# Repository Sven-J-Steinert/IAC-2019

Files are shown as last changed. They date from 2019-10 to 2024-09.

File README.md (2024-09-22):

# Showcase for Satellite Routines
Developed for Telespazio VEGA. Presented on the International Astronautical Congress ( 2019 | Washington, D.C., USA )<br>
This setup consists of 3 parts: The [Orbiter](#orbiter) that is circling around the [Groundstation](#groundstation) and the [Node](#node) that connects both to an internet endpoint. Sending commands to the Orbiter as well as pulling the Telemetry from it is only possible while it is in sight of view of the satellite dish. This creates a connected and disconnected timespan in the periodic circling.

# Orbiter
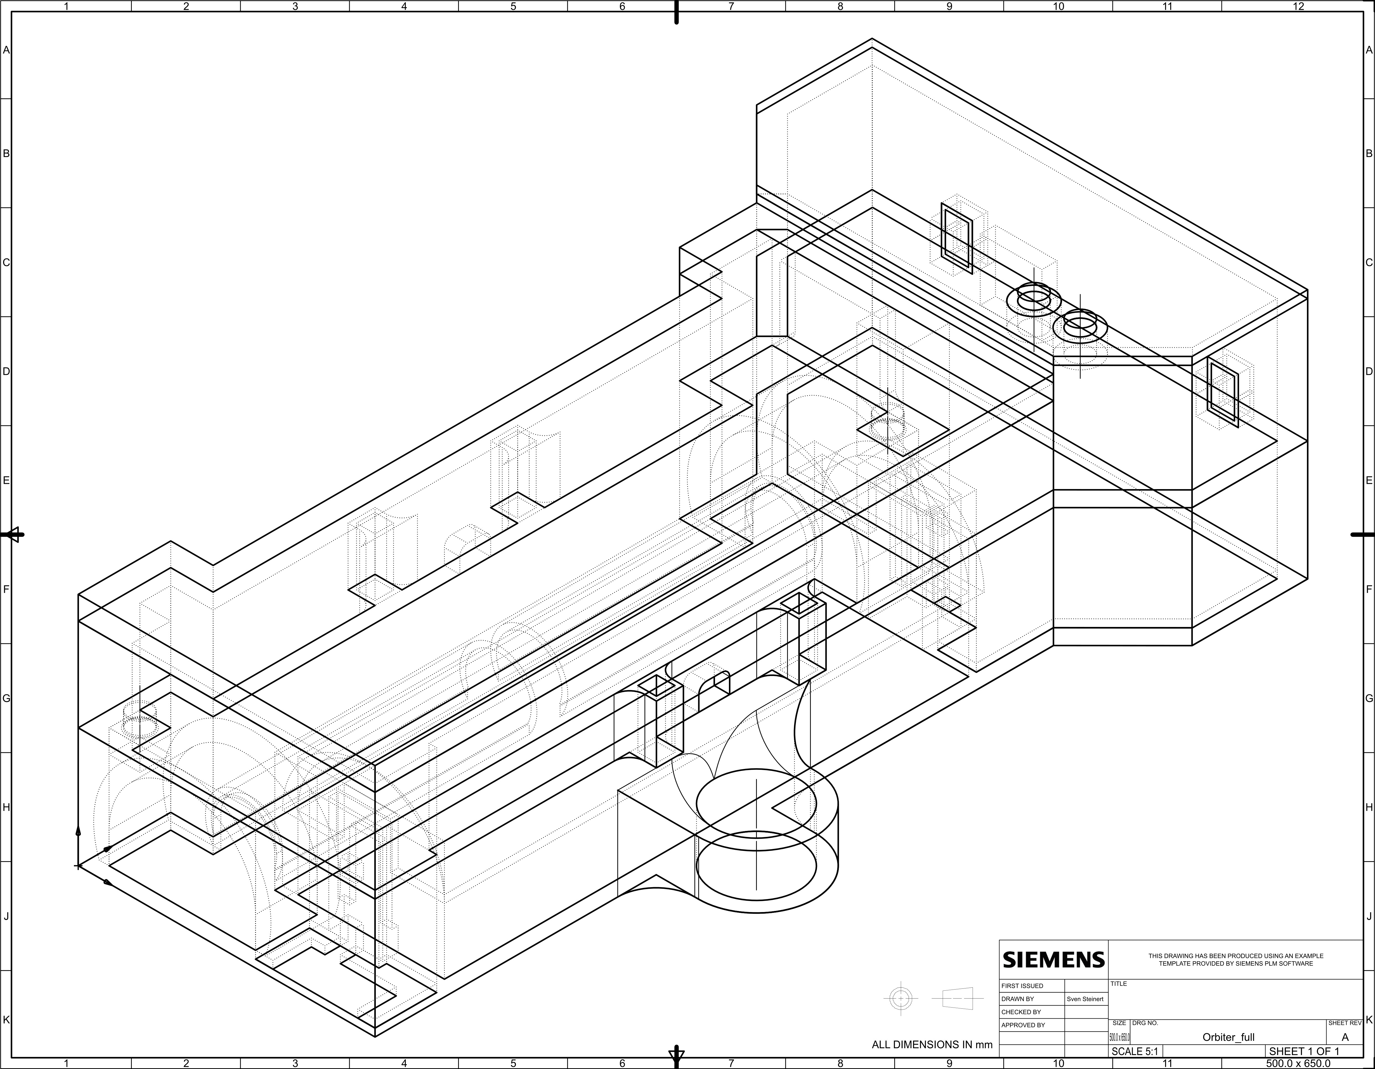
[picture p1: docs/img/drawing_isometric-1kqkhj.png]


While driving a base speed pwm for a circle, the perpendicular regulating is done by minimizing the difference of the two laser distance mesurements to the surface of the globe. Due to the timemanagement, the network calls and the regulation are splitted up on both cores of the ESP32. Since there is no Analog Pin left to use on the Cam version, an Attiny has been set up as an I²C Device that is doing the battery- and solar voltage masurement.

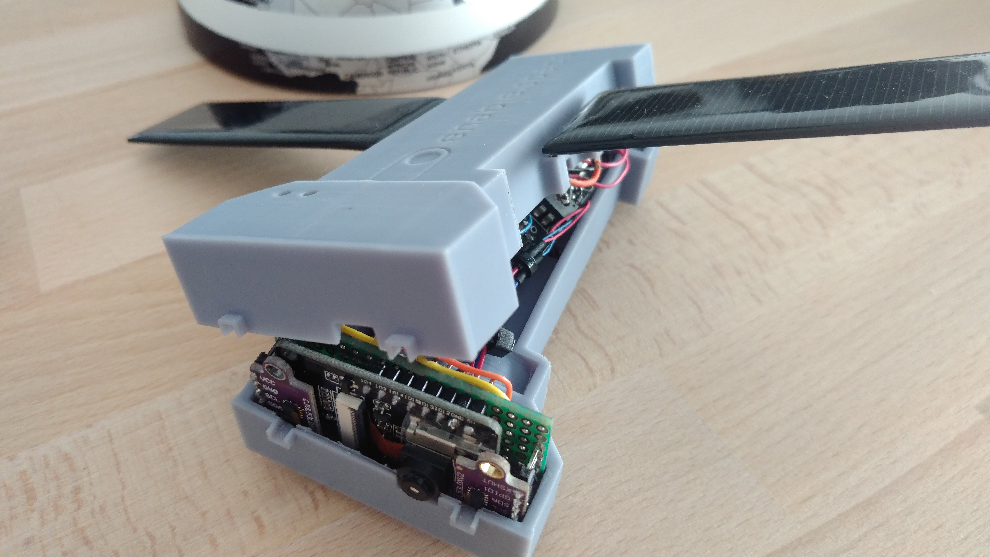
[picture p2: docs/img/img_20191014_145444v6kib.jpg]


## Orbiter Partlist
 
|QTY|	DESCRIPTION	|PART NAME|
| :--- | :--- | :--- |
|1|	DevBoard|	ESP32-CAM OV2640 |
|1|	AVR Microcontroller|	Atmel Attiny85|
|2|	Distance Sensor|VL53L0X 940nm laser|
|2|	Solar Cell|	5.5V 90mm x 30mm 65mA polycrystalline|
|1|	Battery|	Samsung INR18650-35E|
|1|	Votage Converter|	Pololu S9V11F3S5C3 |
|1|	Motor Driver| DRV8833 2-Channel H-Bridge|
|1|	DC Motor| Mini Gearmotor 4,5V 80mA 32rpm|
|1|	Ball-Bearing| L-0123|
|1|	PCB| 30mm x 70mm|
|1|	Switch| ON OFF Toggle|
|2|	Status LED | red, green|
|2|	Resistor| 100 Ω|
|4|	Resistor| 10 kΩ|
|1| Case| 3D SLA Printed |
|2| Wheels| Lasercutted 3mm MDF, rubber coated |

## Orbiter Wiring

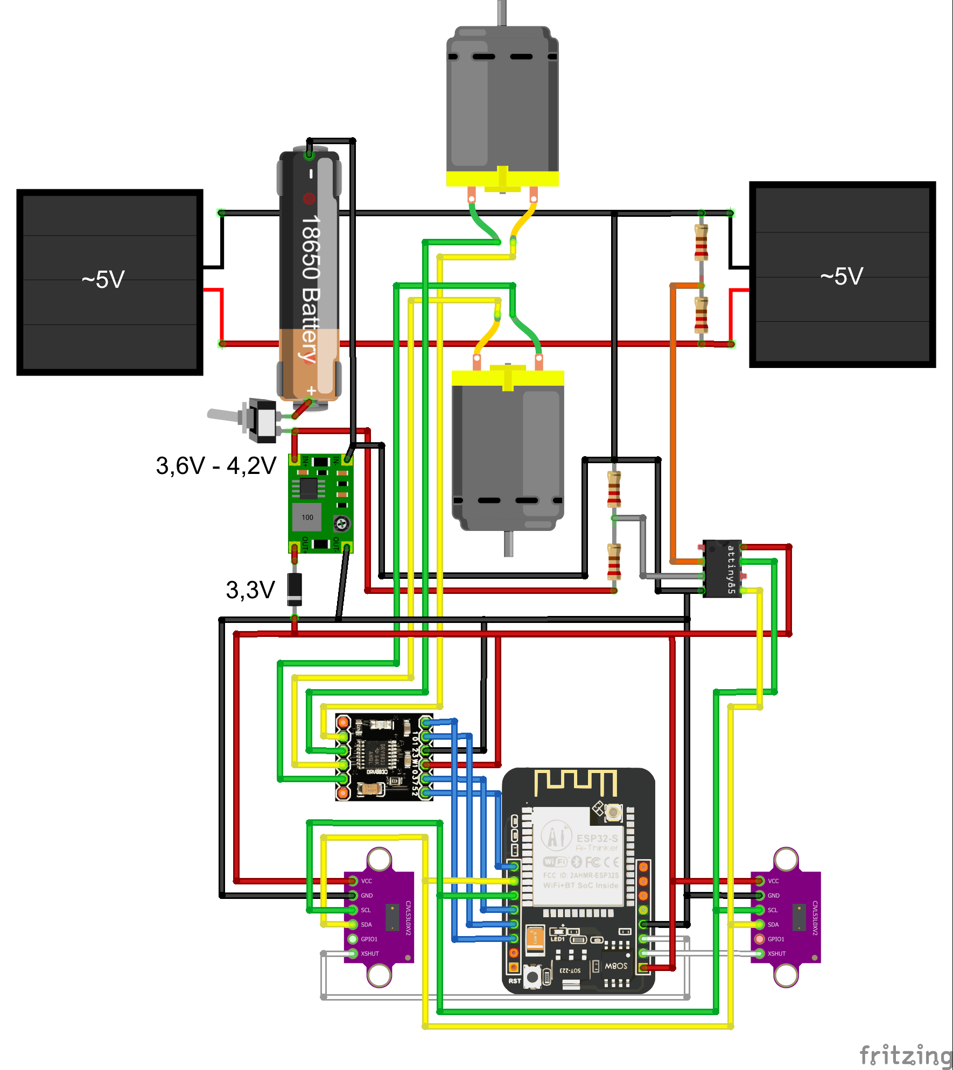
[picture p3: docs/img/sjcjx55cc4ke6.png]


# Groundstation

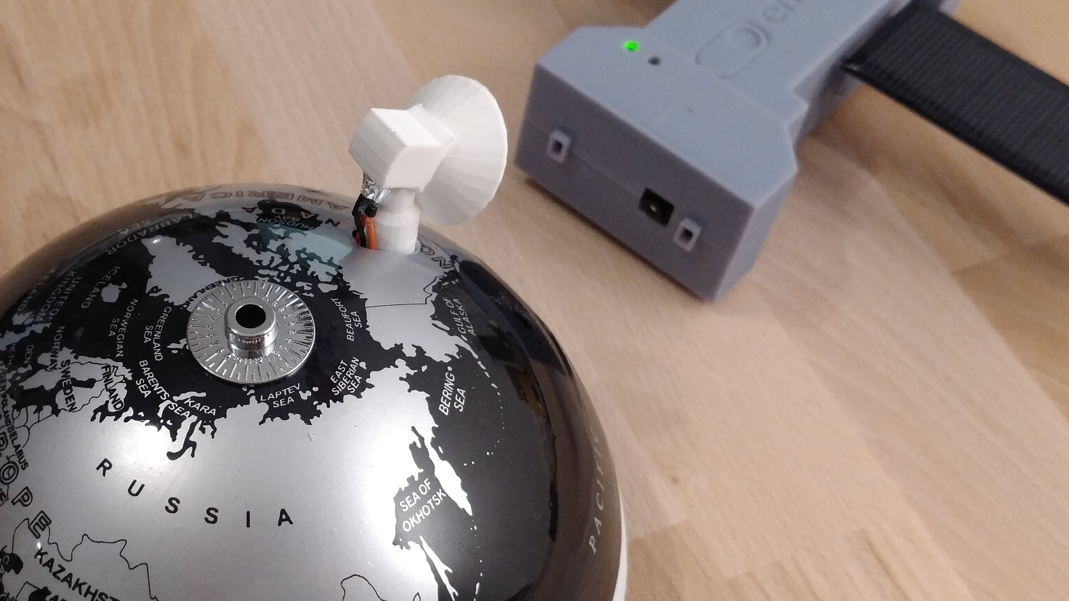
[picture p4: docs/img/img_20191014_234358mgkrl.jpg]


The Groundstation contains 2 parts: the foundation where the most hardware is hidden underneath the globe and the satelite dish where an infrared sensor is mounted into. Every time the Orbiter enters the sight of view, the laser mesurements of the Orbiter are triggering the infrared sensor. After detection it switches the insight value on the Node and starts to following the orbiter. On maximum turning angle or loss of signal it resets back into starting position for the next pass.

## Groundstation Partlist
 
|QTY|	DESCRIPTION	|PART NAME|
| :--- | :--- | :--- |
|1|	DevBoard|	ESP8266 NodeMCU |
|1| Servo| MG90S metal gear |
|1|	Batteryholder | SMD 18650|
|1|	Battery|	Samsung INR18650-35E|
|1|	Votage Converter|	Pololu S9V11F3S5C3 |
|1| Case | 3D FDM Printed |
|1| Globe | Ø 14cm, white striped |

# Node

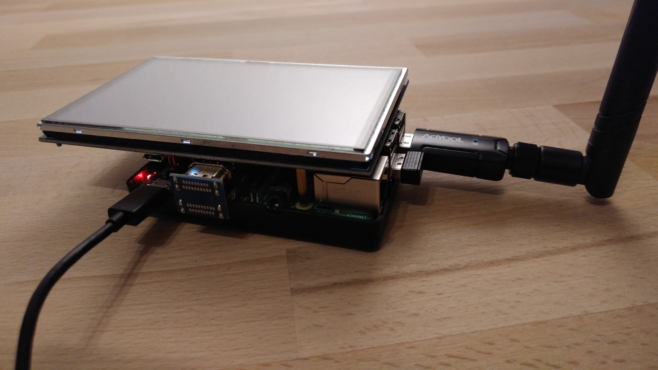
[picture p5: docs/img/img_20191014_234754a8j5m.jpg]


The Node hosts the internal Network as well as the communication endpoints. Telemetry data can either be pushed per POST on an specific index like Elasticsearch or pulled from it via a GET request. Telecomands are done by recieving a POST that will be parsed and executed afterwards. 

## Node Partlist
 
|QTY|	DESCRIPTION	|PART NAME|
| :--- | :--- | :--- |
|1|	single-board Computer|	Raspberry Pi 3 B+ |
|1| Display| 5 inch Display with case |
|1|	Wifi Dongle | Aoyool WiFi Adapter, AP mode|
|1|	Powersupply |	WEYO 5V 3A |
|1|	micro sd card |	SanDisk 32Gb |
|1|	Wireless Keyboard  |	Rii i8 Mini |

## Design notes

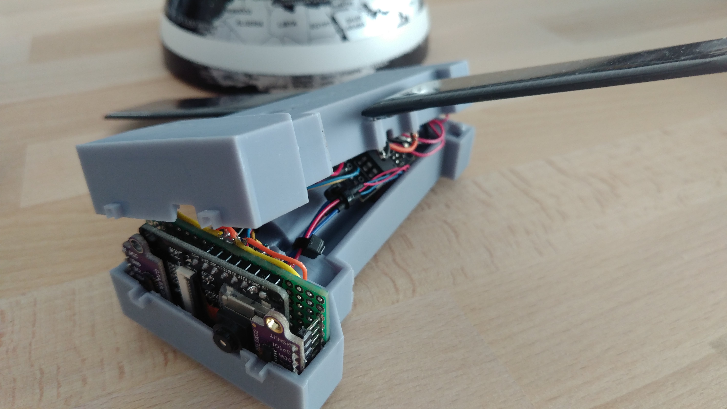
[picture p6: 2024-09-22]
docs/img/img_20191014_1454398wjwb.jpg

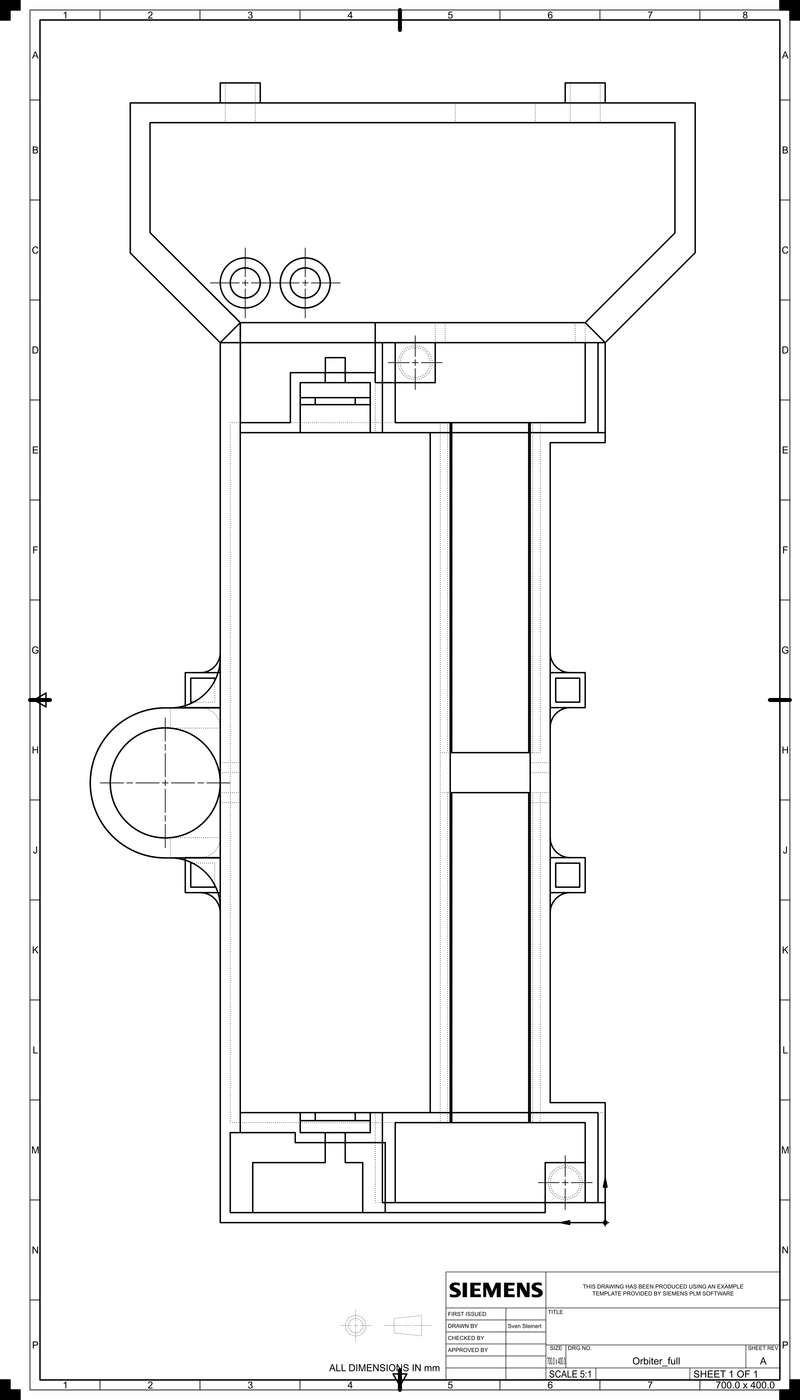
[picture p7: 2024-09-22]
docs/img/drawing_bottom_vert-1m2jxk.png

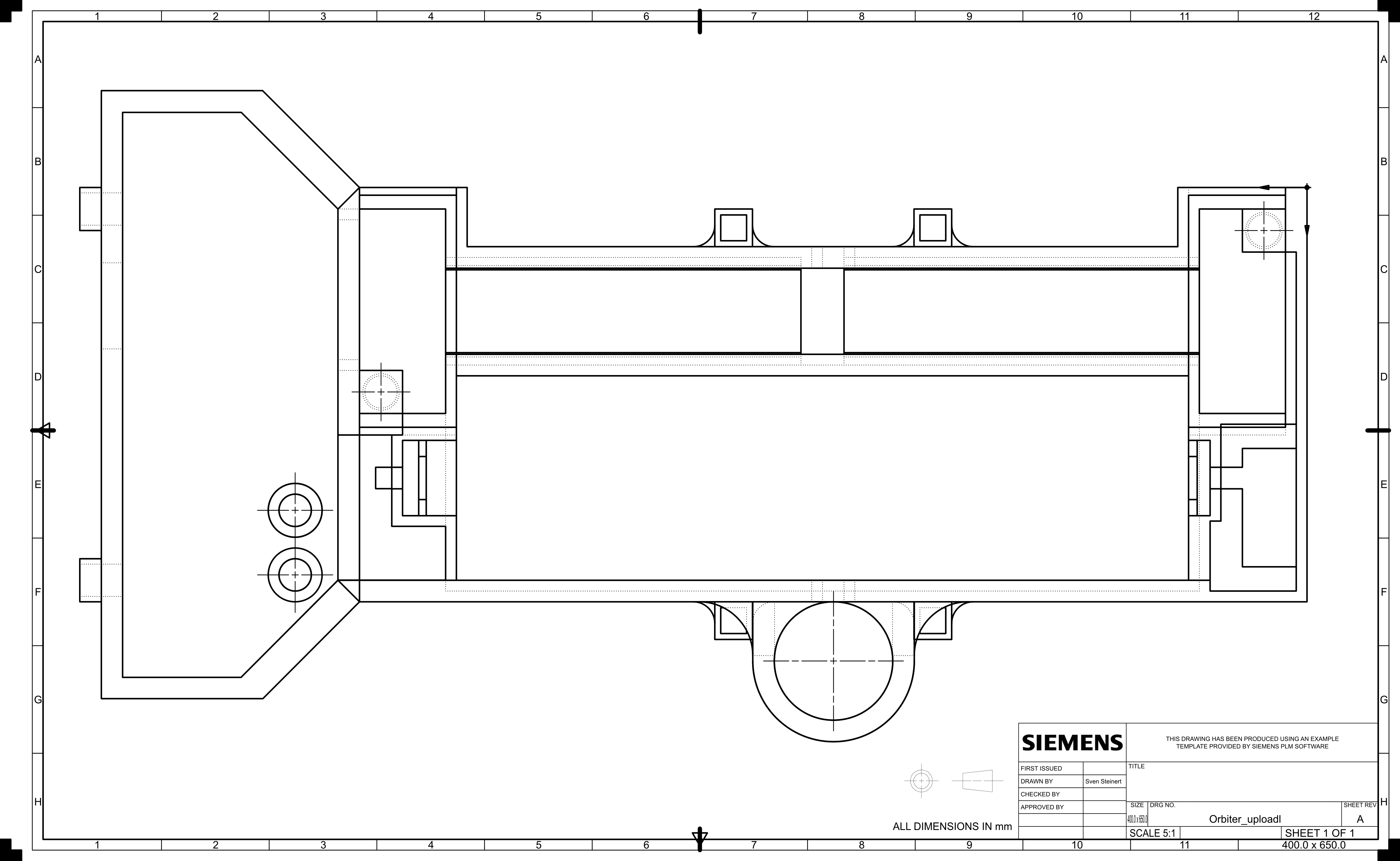
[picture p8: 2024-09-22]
docs/img/drawing_bottom-1pwkzv.png

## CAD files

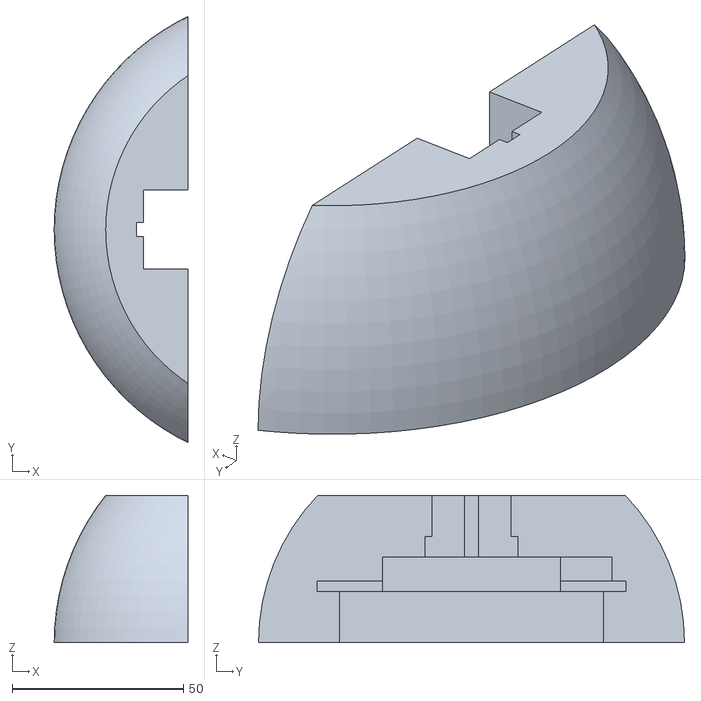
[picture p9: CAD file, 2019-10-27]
GroundStation/Foundation.stl
39.0 x 124.3 x 43.0

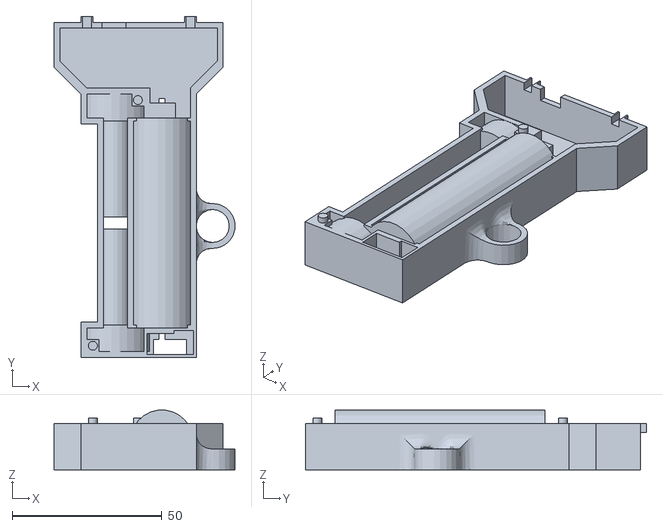
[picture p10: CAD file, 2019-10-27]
Orbiter/Frame.stl
60.4 x 114.0 x 19.9

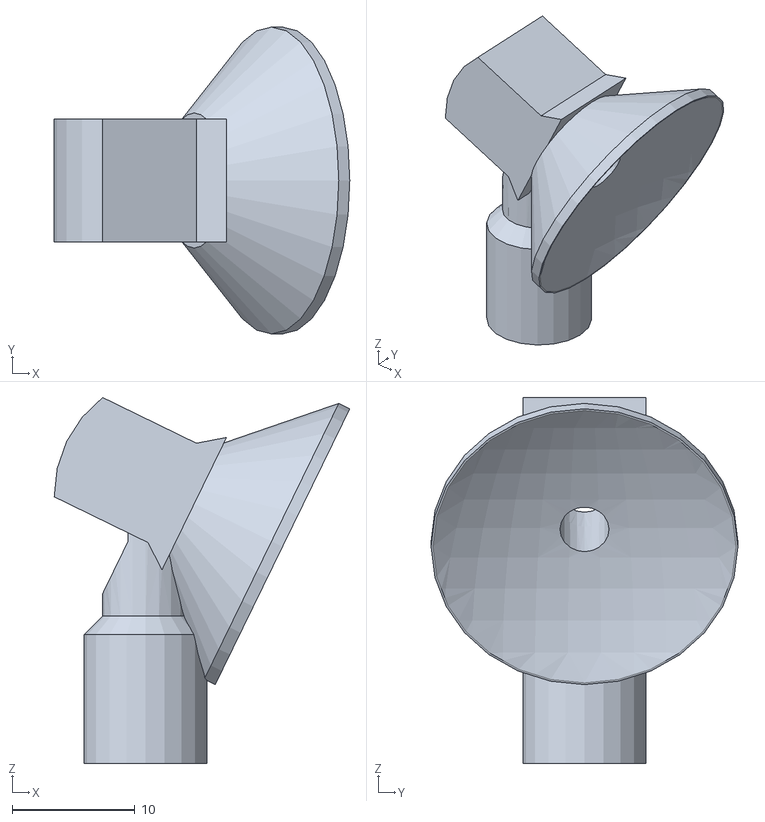
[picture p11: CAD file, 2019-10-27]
GroundStation/Satellite_dish.stl
24.1 x 25.0 x 29.8

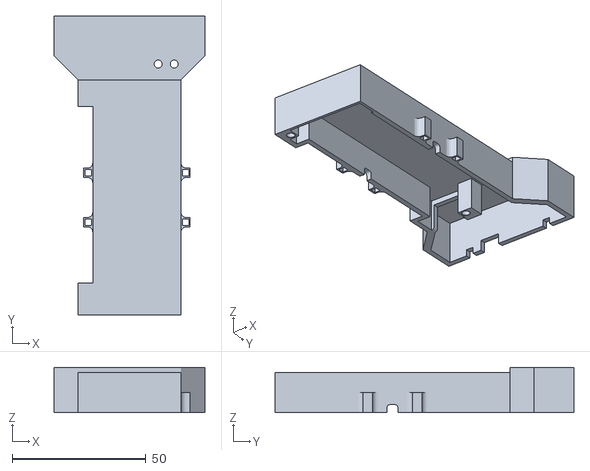
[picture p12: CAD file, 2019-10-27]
Orbiter/Cover.stl
56.5 x 112.0 x 17.0

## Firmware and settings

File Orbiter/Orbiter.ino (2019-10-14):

#include <WiFi.h>
#include <WiFiClient.h>
#include <WebServer.h>
#include <ESPmDNS.h>
#include <Update.h>
#include <Wire.h>
#include <VL53L0X.h>

VL53L0X sensorR;
VL53L0X sensorL;

#define led1 15
#define led2 13
#define in2 12
#define in4 4

const int freq = 50000;
const int M1FChannel = 0, M2FChannel = 1;
const int resolution = 8;

byte pwmI, pwmA ;
int distR, distL, dd=5, calibR = 0,calibL = 0, offsetR = 43, offsetL = 60;
int bat,sol, imgcount=0, psize;
byte bb[8],bc[8], metab[6] ;
byte tcmode=0, tctype=0, tctime=0;
bool lowOrbit=true, picavail=false, insight=false;

unsigned long currenttime,targettime,lasttime=0;
unsigned long check_wifi = 20000;

WiFiUDP udp;
char incomingPacket[7];  // buffer for incoming packets

IPAddress ServerIP(192,168,4,1);

const char* host = "esp32";
const char* ssid = "PiFi.internal";
const char* password = "letmeaccessyourdata";

WebServer server(80);

/*
 * Server Index Page
 */
const char* serverIndex = 
"<script src='https://ajax.googleapis.com/ajax/libs/jquery/3.2.1/jquery.min.js'></script>"
"<form method='POST' action='#' enctype='multipart/form-data' id='upload_form'>"
"<p>Orbiter esp32-webupdate</p>"
   "<input type='file' name='update'>"
        "<input type='submit' value='Update'>"
    "</form>"
 "<div id='prg'>progress: 0%</div>"
 "<script>"
  "$('form').submit(function(e){"
  "e.preventDefault();"
  "var form = $('#upload_form')[0];"
  "var data = new FormData(form);"
  " $.ajax({"
  "url: '/update',"
  "type: 'POST',"
  "data: data,"
  "contentType: false,"
  "processData:false,"
  "xhr: function() {"
  "var xhr = new window.XMLHttpRequest();"
  "xhr.upload.addEventListener('progress', function(evt) {"
  "if (evt.lengthComputable) {"
  "var per = evt.loaded / evt.total;"
  "$('#prg').html('progress: ' + Math.round(per*100) + '%');"
  "}"
  "}, false);"
  "return xhr;"
  "},"
  "success:function(d, s) {"
  "console.log('success!')" 
 "},"
 "error: function (a, b, c) {"
 "}"
 "});"
 "});"
 "</script>";

void intToByte (){
 bc[0]= (bat >> 24) & 0xFF;
 bc[1]= (bat >> 16) & 0xFF;
 bc[2]= (bat >> 8) & 0xFF;
 bc[3]= bat  & 0xFF;
 bc[4]= (sol >> 24) & 0xFF;
 bc[5]= (sol >> 16) & 0xFF;
 bc[6]= (sol >> 8) & 0xFF;
 bc[7]= sol  & 0xFF;
}

void ByteToint (){
bat = (uint32_t) bb[0] << 24;
bat |=  (uint32_t) bb[1] << 16;
bat |= (uint32_t) bb[2] << 8;
bat |= (uint32_t) bb[3]; 

sol = (uint32_t) bb[4] << 24;
sol |=  (uint32_t) bb[5] << 16;
sol |= (uint32_t) bb[6] << 8;
sol |= (uint32_t) bb[7]; 

}

TaskHandle_t Task1;

void setup(void) {

  pinMode(led1, OUTPUT); 
  pinMode(led2, OUTPUT); 
  pinMode(0, OUTPUT);
  pinMode(16, OUTPUT);


  WiFi.disconnect(true);
  delay(500);
  //register event handler
  WiFi.mode(WIFI_STA);
  delay(1000);
  //Initiate connection
  WiFi.begin(ssid, password);
 
  
  /*use mdns for host name resolution*/
  if (!MDNS.begin(host)) { //http://esp32.local
    while (1) {
      delay(1000);
    }
  }
  
  /*return index page which is stored in serverIndex */
  server.on("/", HTTP_GET, []() {
    server.sendHeader("Connection", "close");
    server.send(200, "text/html", serverIndex);
  });
  /*handling uploading firmware file */
  server.on("/update", HTTP_POST, []() {
    server.sendHeader("Connection", "close");
    server.send(200, "text/plain", (Update.hasError()) ? "FAIL" : "OK");
    ESP.restart();
  }, []() {
    HTTPUpload& upload = server.upload();
    if (upload.status == UPLOAD_FILE_START) {
      if (!Update.begin(UPDATE_SIZE_UNKNOWN)) { //start with max available size
      }
    } else if (upload.status == UPLOAD_FILE_WRITE) {
      /* flashing firmware to ESP*/
      if (Update.write(upload.buf, upload.currentSize) != upload.currentSize) {
      }
    } else if (upload.status == UPLOAD_FILE_END) {
      if (Update.end(true)) { //true to set the size to the current progress
      } else {
      }
    }
  });
  server.begin();
  
  ledcSetup(M1FChannel, freq, resolution);
  ledcSetup(M2FChannel, freq, resolution);
 
  ledcAttachPin(in2, M1FChannel);
  ledcAttachPin(in4, M2FChannel);
  
  ledcWrite(M1FChannel, 0);
  ledcWrite(M2FChannel, 0);
  
  digitalWrite(0, LOW);
  digitalWrite(16, LOW);

  //initialize 2 Distance-Sensors
  Wire.begin(2,14);
  digitalWrite(16, HIGH);
  delay(150);
  sensorR.init(true);
  delay(100);
  sensorR.setMeasurementTimingBudget(200000);
  sensorR.setAddress((uint8_t)25);
  digitalWrite(0, HIGH);
  delay(150);
  sensorL.init(true);
  delay(100);
  sensorL.setMeasurementTimingBudget(200000);

  udp.begin(WiFi.localIP(),2000);

//calibration
digitalWrite(led2, HIGH);
calibR=0;
calibL=0;
 for (int i = 0; i < 10; i++) {
    calibR=calibR+sensorR.readRangeSingleMillimeters();
    delay(200);
    calibL=calibL+sensorL.readRangeSingleMillimeters();
    delay(200);
  }
  offsetR = (calibR/10)-20;
  offsetL = (calibL/10)-20;

if (offsetR>200 || offsetL>200){
  calibR=0;
  calibL=0;
  for (int i = 0; i < 10; i++) {
    calibR=calibR+sensorR.readRangeSingleMillimeters();
    delay(200);
    calibL=calibL+sensorL.readRangeSingleMillimeters();
    delay(200);
  }
  offsetR = (calibR/10)-15;
  offsetL = (calibL/10)-15;
}
  
  byte oR[4],oL[4];
 oR[0]= (offsetR >> 24) & 0xFF;
 oR[1]= (offsetR >> 16) & 0xFF;
 oR[2]= (offsetR >> 8) & 0xFF;
 oR[3]= offsetR  & 0xFF;
 oL[0]= (offsetL >> 24) & 0xFF;
 oL[1]= (offsetL >> 16) & 0xFF;
 oL[2]= (offsetL >> 8) & 0xFF;
 oL[3]= offsetL  & 0xFF;
 
 udp.beginPacket(ServerIP, 2005);
 udp.write(oR[1]);
 udp.write(oR[2]);
 udp.write(oR[2]);
 udp.write(oR[3]);
 udp.endPacket();
 udp.flush();
 delay(100);
 udp.beginPacket(ServerIP, 2005);
 udp.write(oL[1]);
 udp.write(oL[2]);
 udp.write(oL[2]);
 udp.write(oL[3]);
 udp.endPacket();
 udp.flush();
 delay(100);
digitalWrite(led2, LOW);
delay(2000);

    digitalWrite(led1, HIGH);
    digitalWrite(led2, HIGH);

// Go to Zero , Updatable
while (dd>3 || dd<-3) {
   server.handleClient();
    distR = sensorR.readRangeSingleMillimeters()-offsetR;
    delay(200);
    distL = sensorL.readRangeSingleMillimeters()-offsetL;
    delay(200);
    dd = distR -distL;
    if ((dd<3)&&(dd>-3)){
      ledcWrite(M1FChannel, 0);
      ledcWrite(M2FChannel, 0);
    }
    if (dd>3){
      ledcWrite(M1FChannel, 70);
      ledcWrite(M2FChannel, 0);
    }
    if (dd<-3){
      ledcWrite(M1FChannel, 0);
      ledcWrite(M2FChannel, 70);
    }
}
      ledcWrite(M1FChannel, 0);
      ledcWrite(M2FChannel, 0);
  digitalWrite(led1, LOW);
  digitalWrite(led2, LOW);
  delay(500);


  xTaskCreatePinnedToCore(
                    Task1code,   // Task function. 
                    "Task1",     // name of task. 
                    10000,       // Stack size of task 
                    NULL,        // parameter of the task 
                    1,           // priority of the task 
                    &Task1,      // Task handle to keep track of created task 
                    1);          // pin task to core 1  

                   
}

void loop(void) {
    
    Wire.requestFrom(0x50, 8); // request 1 byte from slave device address 4
    byte u=0;
    while(Wire.available()) // slave may send less than requested
      {
        bb[u]= Wire.read();
        u++;
      }
 
    ByteToint();
    bat=map(bat,0,1023,0,6600);
    sol=map(sol,0,1023,0,6600);
    intToByte();
    delay(10);
   
    distR = sensorR.readRangeSingleMillimeters()-offsetR;
    delay(220);
    distL = sensorL.readRangeSingleMillimeters()-offsetL;
    delay(220);
    dd = distR-distL;
    
    pwmI = 70;
    pwmA = 135; 
    //pwmA = 130;  
    
    if (dd>5){
      int val = pwmA +(4*dd);
      pwmA = round( min(val, 255));
    }else if (dd<-5){
      int val = pwmI +(-4*dd);
      pwmI = round( min(val, 255));
    }
    
    ledcWrite(M1FChannel, pwmA);
    ledcWrite(M2FChannel, pwmI);

if (insight){
  digitalWrite(led2, HIGH);
}else{
  digitalWrite(led2, LOW);
}

// run TC 
currenttime = millis();
if (currenttime > targettime){
  if (tcmode == 1){
    digitalWrite(led1, HIGH);
        //move to low Orbit
             ledcWrite(M1FChannel, 255);
             ledcWrite(M2FChannel, 70);
             delay(4000);
        ledcWrite(M1FChannel, 100);
        ledcWrite(M2FChannel, 100);
        delay(2000);
        digitalWrite(led1, LOW);
    tcmode = 0;
    tctype = 0;
    tctime = 0;
  }
 if (tcmode == 3){
  digitalWrite(led1, HIGH);
        //move to high Orbit
            ledcWrite(M1FChannel, 200);
            ledcWrite(M2FChannel, 195);
            delay(2500);
            ledcWrite(M1FChannel, 255);
            ledcWrite(M2FChannel, 70);
            delay(1000);
            digitalWrite(led1, LOW);
    tcmode = 0;
    tctype = 0;
    tctime = 0;
    }
 if (tcmode == 2){
    digitalWrite(led1, HIGH);
    delay(100);
    digitalWrite(led1, LOW);
    delay(50);
    digitalWrite(led1, HIGH);
      imgcount++;
      metab[0]=imgcount;
      if (tctype == 1){
        // photo res = 640x480
        metab[1]=1;
        psize = random(350, 600);
      }
      if (tctype == 2){
        // photo res = 1024x768
        metab[1]=2;
        psize = random(600, 900);
      }
      if (tctype == 3){
        // photo res = 1600x1200
        metab[1]=3;
        psize = random(900, 1500);
      }
      
       metab[2]= (psize >> 24) & 0xFF;
       metab[3]= (psize >> 16) & 0xFF;
       metab[4]= (psize >> 8) & 0xFF;
       metab[5]= psize  & 0xFF;

       picavail=true;

       digitalWrite(led1, LOW);
    tcmode = 0;
    tctype = 0;
    tctime = 0;
    }
    

}
    
}

void Task1code( void * pvParameters ){

  for(;;){

    // reconnects every 2 seconds
  if (millis() > check_wifi) {
    WiFi.disconnect(true);
    WiFi.mode(WIFI_STA);
    WiFi.begin(ssid, password);
    udp.begin(WiFi.localIP(),2000);
    check_wifi = millis() + 2000;
  }
   
    int packetSize = udp.parsePacket();
  if (packetSize){ 
    udp.read(incomingPacket, 7);
    digitalWrite(led1, HIGH);
    delay(100);
    digitalWrite(led1, LOW);
    
   if (String(incomingPacket[0]) == "t"){
    insight = true;
    udp.beginPacket(ServerIP, 2010);
    udp.write(1);
    udp.endPacket();
    udp.flush();
   }else if (String(incomingPacket[0]) == "f"){
    insight = false;
    udp.beginPacket(ServerIP, 2010);
    udp.write(1);
    udp.endPacket();
    udp.flush();
   }else if (tcmode==0){
    // Bitshift char -> byte
    tcmode = incomingPacket[0] - 0x30;
    tctype = incomingPacket[2] - 0x30;
    String x1,x2,x3;
    x1 = String(incomingPacket[4]-0x30);
    x2 = String(incomingPacket[5]-0x30);
    x3 = String(incomingPacket[6]-0x30);
    String myString = x1+x2+x3; 
    tctime = myString.toInt();
    targettime = millis() + tctime*1000;
        // send answer
    udp.beginPacket(ServerIP, 2006);
    udp.write(1);
    udp.endPacket();
    udp.flush();
    }
        // clear 
    incomingPacket[0]=0;
    incomingPacket[1]=0;
    incomingPacket[2]=0;
    incomingPacket[3]=0;
    incomingPacket[4]=0;
    incomingPacket[5]=0;
    incomingPacket[6]=0;
    incomingPacket[7]=0;
    }
    
if (currenttime > lasttime+2000){
// Send TM Bat-Voltage Sol-Voltage
 udp.beginPacket(ServerIP, 2000);
 udp.write(bc[0]);
 udp.write(bc[1]);
 udp.write(bc[2]);
 udp.write(bc[3]);
 udp.endPacket();
 udp.flush();
 delay(100);
udp.beginPacket(ServerIP, 2001);
 udp.write(bc[4]);
 udp.write(bc[5]);
 udp.write(bc[6]);
 udp.write(bc[7]);
 udp.endPacket();
 udp.flush();
 lasttime=millis();
}


if (picavail){
  // send Photo meta
       udp.beginPacket(ServerIP, 2002);
       udp.write(metab[0]);
       udp.write(metab[1]);
       udp.write(metab[2]);
       udp.write(metab[3]);
       udp.write(metab[4]);
       udp.write(metab[5]);
       udp.endPacket();
       udp.flush();
       picavail=false;
}
   
  } 
}

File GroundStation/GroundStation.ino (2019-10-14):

#include <ESP8266WiFi.h>
#include <WiFiUdp.h>
#include <WiFiClient.h>
#include <ESP8266WebServer.h>
#include <ESP8266mDNS.h>
#include <Servo.h>

const char* ssid ="PiFi.internal";
const char* pass ="letmeaccessyourdata";

const char* host = "esp8266-webupdate";

#define IR_PIN 12
#define Servo_PIN 13


unsigned int localPort = 2000; // local port to listen for UDP packets

IPAddress ServerIP(192,168,4,1);
 
// A UDP instance to let us send and receive packets over UDP
WiFiUDP udp;


Servo myservo;  // create servo object to control a servo
int pos = 170;    // variable to store the servo position
byte x;
int i=0,t=0, c=0;
bool ir=false, nostop= false;

unsigned long check_wifi = 5000;

ESP8266WebServer server(80);
const char* serverIndex = "<form method='POST' action='/update' enctype='multipart/form-data'><p>Groundstation esp8266-webupdate</p><input type='file' name='update'><input type='submit' value='Update'></form>";


void setup()
{
  pinMode(IR_PIN, INPUT);
  myservo.attach(Servo_PIN); 
  myservo.write(pos);
  
  Serial.begin(115200);
    Serial.println();
 
  initNetwork();
  
if (WiFi.waitForConnectResult() == WL_CONNECTED) {
    MDNS.begin(host);
    server.on("/", HTTP_GET, []() {
      server.sendHeader("Connection", "close");
      server.send(200, "text/html", serverIndex);
    });
    server.on("/update", HTTP_POST, []() {
      server.sendHeader("Connection", "close");
      server.send(200, "text/plain", (Update.hasError()) ? "FAIL" : "OK");
      ESP.restart();
    }, []() {
      HTTPUpload& upload = server.upload();
      if (upload.status == UPLOAD_FILE_START) {
        Serial.setDebugOutput(true);
        WiFiUDP::stopAll();
        Serial.printf("Update: %s\n", upload.filename.c_str());
        uint32_t maxSketchSpace = (ESP.getFreeSketchSpace() - 0x1000) & 0xFFFFF000;
        if (!Update.begin(maxSketchSpace)) { //start with max available size
          Update.printError(Serial);
        }
      } else if (upload.status == UPLOAD_FILE_WRITE) {
        if (Update.write(upload.buf, upload.currentSize) != upload.currentSize) {
          Update.printError(Serial);
        }
      } else if (upload.status == UPLOAD_FILE_END) {
        if (Update.end(true)) { //true to set the size to the current progress
          Serial.printf("Update Success: %u\nRebooting...\n", upload.totalSize);
        } else {
          Update.printError(Serial);
        }
        Serial.setDebugOutput(false);
      }
      yield();
    });
    server.begin();
    MDNS.addService("http", "tcp", 80);

    Serial.printf("Ready! Open http://%s.local in your browser\n", host);
  } else {
    Serial.println("WiFi Failed");
  }

    //Start UDP
  Serial.println("Starting UDP");
  udp.begin(localPort);
  Serial.print("Local port: ");
  Serial.println(udp.localPort());
  
   pos=170;
   myservo.write(pos);

}




void loop()
{
  // if wifi is down, try reconnecting every 5 seconds
  if ((WiFi.status() != WL_CONNECTED) && (millis() > check_wifi)) {
    WiFi.disconnect(true);
    WiFi.mode(WIFI_STA);
    WiFi.begin(ssid, pass);
    udp.begin(localPort);
    check_wifi = millis() + 5000;
  }


// get IR
   x = digitalRead(12);
  // IR refresh
  if (x == 0){
    ir=true;
    i=0;
   }
   // IR loss
if ((x == 1)&&(i>=150)){
  ir=false;
}
  i++;
  // connected count
if ((ir==true) || nostop){
  t++;
  c++;
}


if (((ir == true)&&(t>=10)&&(c>=120)) || ((nostop)&&(t>=10)) ){
  // make Servo Steps
    myservo.write(pos);              
    pos -= 1;
    t=0;                     
  if(pos <= 6){
  // finish routine
    pos=170;
    myservo.write(pos); 
    t=0;i=0;c=0;
    nostop = false;
    for (int a = 0; a < 5; a++) {
     udp.beginPacket(ServerIP, 1999);
     udp.write(1);
     udp.endPacket();
     udp.flush();
  }
  }
}

if ((pos < 160)&&(pos > 155)){
 udp.beginPacket(ServerIP, 1998);
 udp.write(1);
 udp.endPacket();
 udp.flush();
 nostop = true;
}

if (ir == false){
 // pos=170;
 //  myservo.write(pos);
   c=0;
}

  server.handleClient();
  MDNS.update();
  delay(20);

}




void initNetwork()
{
  WiFi.mode(WIFI_STA);
  WiFi.begin(ssid, pass);
  while (WiFi.status() != WL_CONNECTED) {
    Serial.print('.');
    delay(500);
  }
  Serial.print("Connected! IP address: ");
  Serial.println(WiFi.localIP());
  Serial.printf("UDP server on port %d\n", localPort);
  udp.begin(localPort);
}
